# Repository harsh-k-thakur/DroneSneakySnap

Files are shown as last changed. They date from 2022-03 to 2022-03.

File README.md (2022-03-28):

# DroneSneakySnap

This project was build as a part of my quarter studies at University of California San Diego.
This project was executed in a group of two. My partner Rye Gleason and I shared the idea and code together to build an end product. 

This project started with understanding dynamics and kinematics of drone. How does Roll, Pitch, Yaw and Throttle works in an open space.

Once I understood the basic dynamics of the drone. 

I started building with the Hardware. For this I used '''Fusion360''' to create new libraries for my IMU, LEDS and Resistors.
Some of the libraries were directly provided to us, and which are readily available in Fusion360 as well. Thus, understanding the basic schematic of a particular part and utilizing the knowledge of that part to integrate in the main project was important. 
You can see datasheet and schmetics of different electronics component under [datasheeet]('/datasheeet/') folder.

All the necessary things related to Hardware are available in [Hardware]('/Hardware/') folder. Things like Schematics, Fusion360 files, Gerber Files are located in the [Hardware]('/Hardware/') folder. Feel free to check those out.

Once done with Hardware, we started working on software. 
While our Printed Circuit Board (PCB) got printed and came back to us we were given a temporary quadcopter in order to start with programming. 
For the software we had Atmega Arduino Micro-controller on the Flight Controller Board. 
Started the project with basic communication between the remote and the quadcopter using Radio Frequency, testing each motors individually works at different spped using Pulse Width Modulation (PWM).
Integrated throttle control from remote and RF together so that we can control the speed using the remote.

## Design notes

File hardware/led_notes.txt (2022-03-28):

Red LEDs: 
1.95V forward voltage
100 Ohm resistor
22.5 mA current
50.6 mW dissipated by resistor

Blue LEDs:
3.3V forward voltage
51 Ohm resistor
17.6 mA current
15.8 mW dissipated by resistor

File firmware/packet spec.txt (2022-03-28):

1 byte magicnum

1 bit enable
1 bit single/multi motor
2 bit motor select
4 bit parameter select

4 byte parameter value
4 bytes setpoint

parameter options:
1 none
9 PID
1 complementary gain
1 gyro highpass
1 XL LP cutoff

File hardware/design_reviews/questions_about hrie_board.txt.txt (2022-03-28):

Questions from Sample Check LIst

1. Antenna and Antenna Driver
	Everthing looks good for this section

2. Power and Ground
	a. The VBAT and BAT_GND, around motors is less than 3mm, if you dont require current there you can just make your two layers small.
	b. Also you have less than 3mm around your mounting hole towards the board. I don't know if this going to create an issue(we can confirm with professor).
	c. PWM4 line cuts the layer 15 into two planes.

3. IMU
	Everthing looks good for this section

4. Headers
	a. No names gives to breakout header.

5. Microcontroller
	Everthing looks good for this section

6. Power Supply
	2V5 power plane is not under the voltage regulator

7. Motor Drivers
	Everthing looks good for this section
	Can you check thickness of nets the motor driver for me (Rye)!

8. Aesthetics
	a. Board looks fine, but increasing the thickness at the end of the board where motors connects, would help you survive the damage.
	b. Reference designators overlaps near IMU, microcontroller and volatage regulator, try if you can make it work.

9. Mechanical
	Everthing looks good for this section

10. LEDs

11. Checks
	I think there is a blob under antenna which is not required.

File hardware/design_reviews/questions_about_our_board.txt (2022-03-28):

****************
Sample Checklist
****************

Is the trace between the balun and the antenna short (no longer than the corresponding trace in the reference design)?
--> Eaglint wants 6mm, did this pass the auto check?

Is it okay for the antenna to be not on the edge of the board?
--> Signal integrity may be compromised by electrical parts around it, particularly the two parts of the board below the antenna

Should the cutout include part of the MCU?
--> Discussed with us during class

Is the FTDI header oriented so the silkscreen is labels for the pins are on the board and the pins will protrude off the board?
--> Not close to the edge of the board

Does the layout look nice?
--> You can make layer 2 and 15 pours cover the whole board, otherwise the color will be different near the propellor

Double check header orientation
--> Looks different than ours, not sure if that matters

Mechanical ring width
--> Width is 3.2mm, which is much thicker than requirement (1.7mm). Could make it thinner for better propellor clearance.

**********
DRC CHECKS
**********

Trace width error was approved for the balun
--> On ADRV pin in B1, the trace width underneath is much bigger than Professor's video example

Trace width error on pin 58 for the MCU
--> Maybe rewire that pin

****
LEDS
****

24 extra LEDS might be super bright if they can't be dimmed
--> Maybe consider a potentiometer to control brightness
--> Also, resistors are calculated based on max VBAT (4.2V)

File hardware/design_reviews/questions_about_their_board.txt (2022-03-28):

Reviewers: SneakySnap
Harsh (hthakur@ucsd.edu)
Rye (njgleaso@ucsd.edu)
Reviewees: DW
William (wis003@ucsd.edu)
Mingyang (miliu@ucsd.edu)

Questions from Sample Check LIst

1. Antenna and Antenna Driver
	Will the copper DW close to the antenna cause interferece? According to me yes.

2. Power and Ground
	a. The VBAT and BAT_GND, around motors is less than 3mm, if you dont require current there you can just make your two layers small.

3. IMU
	Everthing looks good for this section

4. Headers
	a. No names gives to breakout header. No silkscreen labels on your programming header

5. Microcontroller
	Everthing looks good for this section

6. Power Supply
	2V5 power plane is not under the voltage regulator

7. Motor Drivers
	Everthing looks good for this section

8. Aesthetics
	a. Board looks fine, but increasing the thickness at the end of the board where motors connects, would help you survive the damage.
	b. Reference designators overlaps near IMU, microcontroller and volatage regulator, try if you can make it work. Names and values for C12 and nearby capacitors are a mess, same for C16. C1 and C2 labels will be hidden by the parts you're placing there

9. Mechanical
	a. Grommet ring to board connection is very thin, are you sure it'll withstand a crash?

10. LEDs
	Everthing looks good for this section		

11. Checks
	I think there is a blob under antenna which is not required.

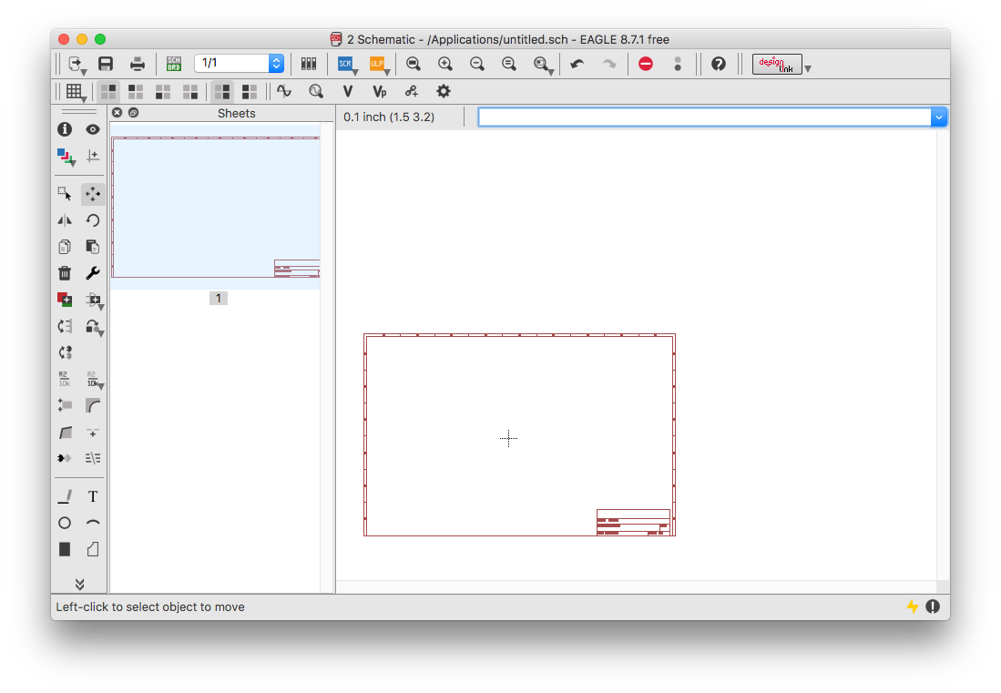
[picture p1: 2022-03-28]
labs/Introduction-To-Eagle/images/schematic4.png

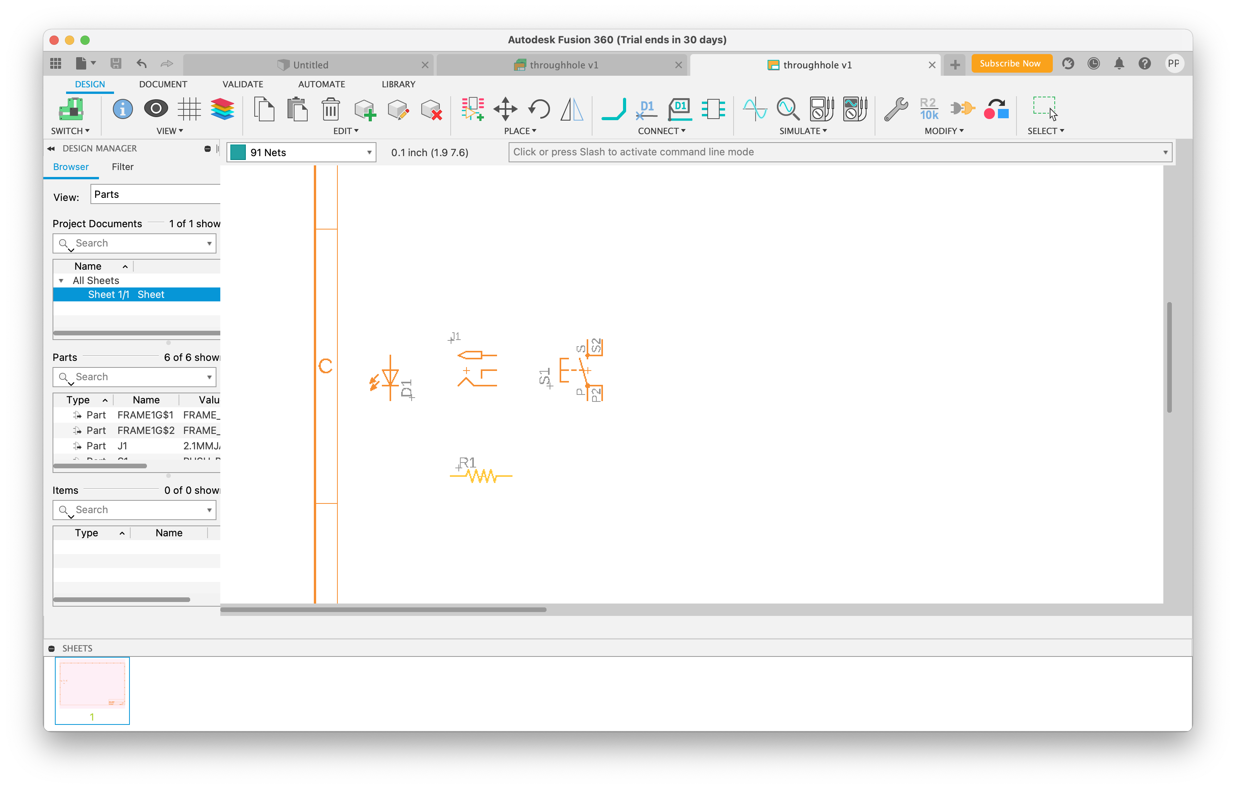
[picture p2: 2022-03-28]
labs/Introduction-To-Eagle/images/schematic6_f360.png

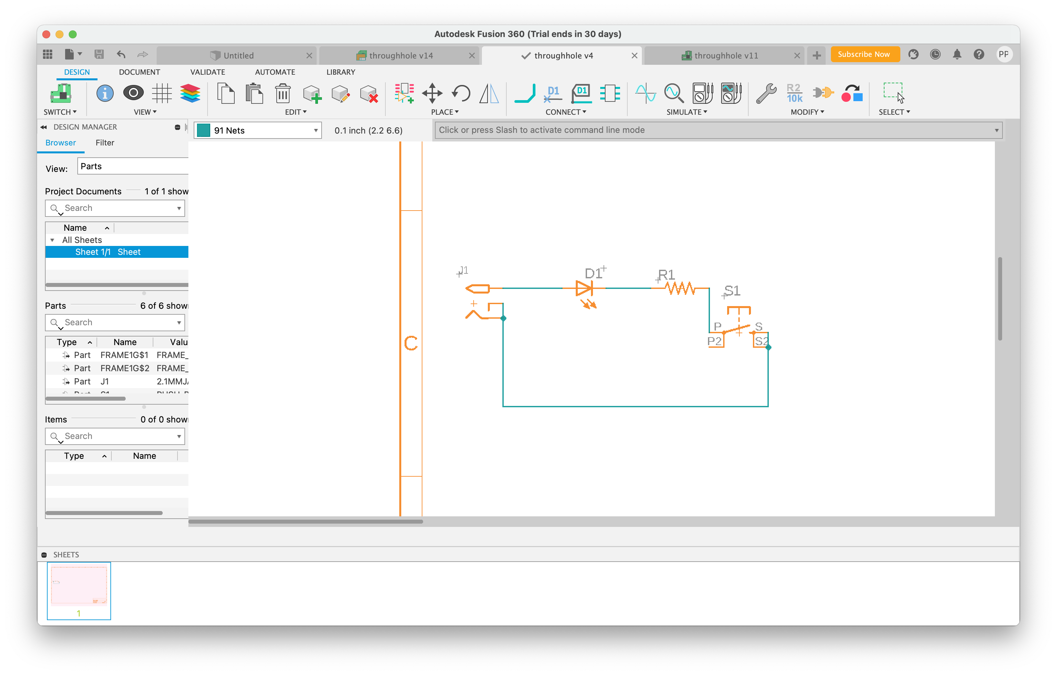
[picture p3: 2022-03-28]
labs/Introduction-To-Eagle/images/schematic12_f360.png

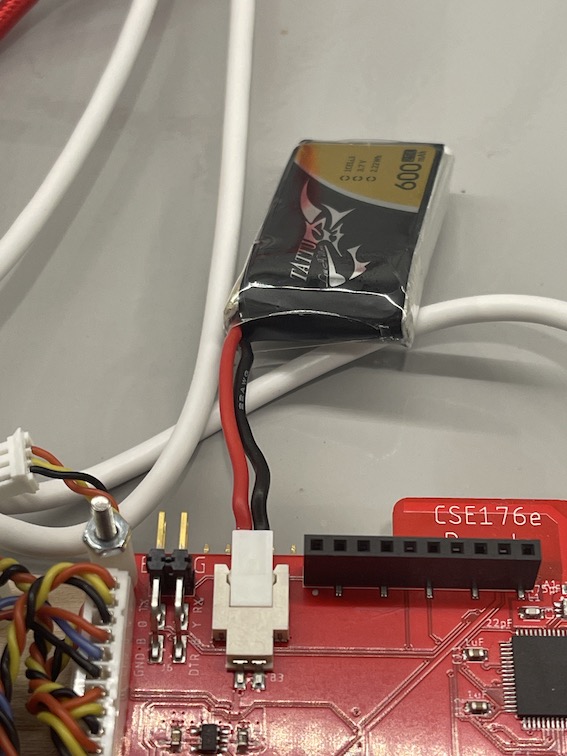
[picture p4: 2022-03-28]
labs/Programming-The-Hardware/images/connect-battery.jpg

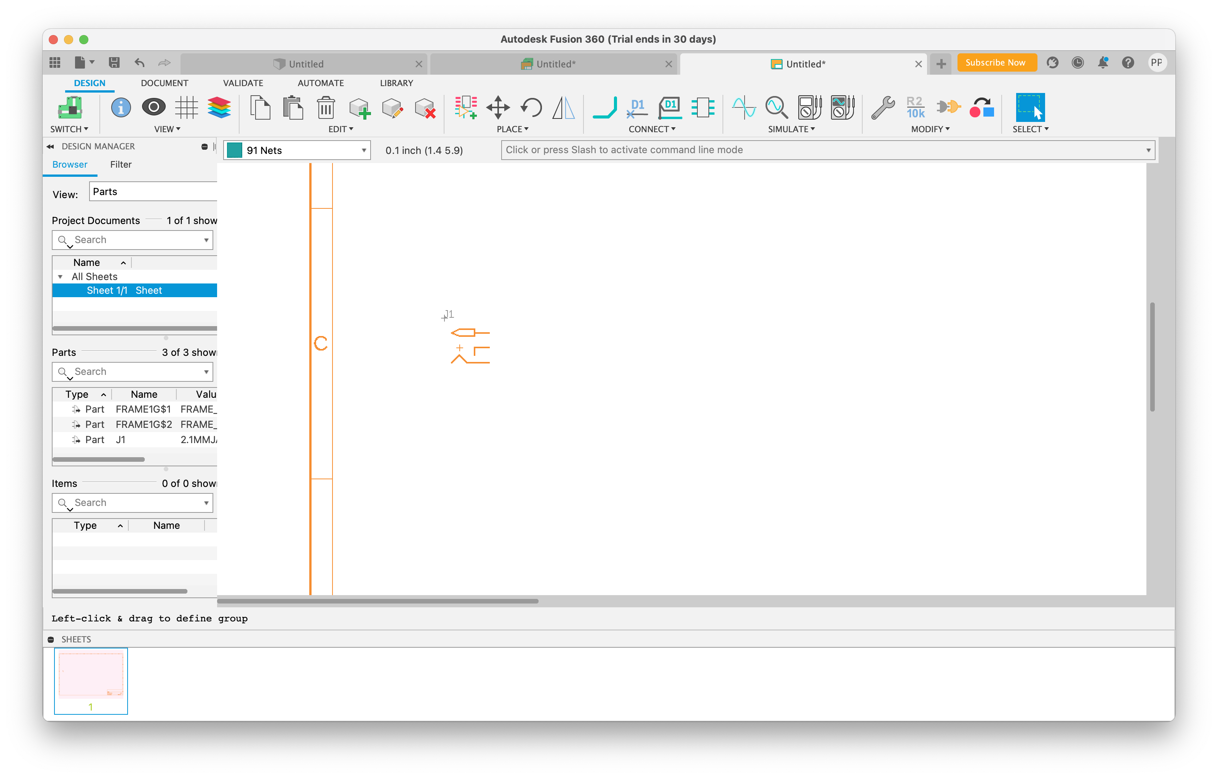
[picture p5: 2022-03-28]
labs/Introduction-To-Eagle/images/schematic5_f360.png

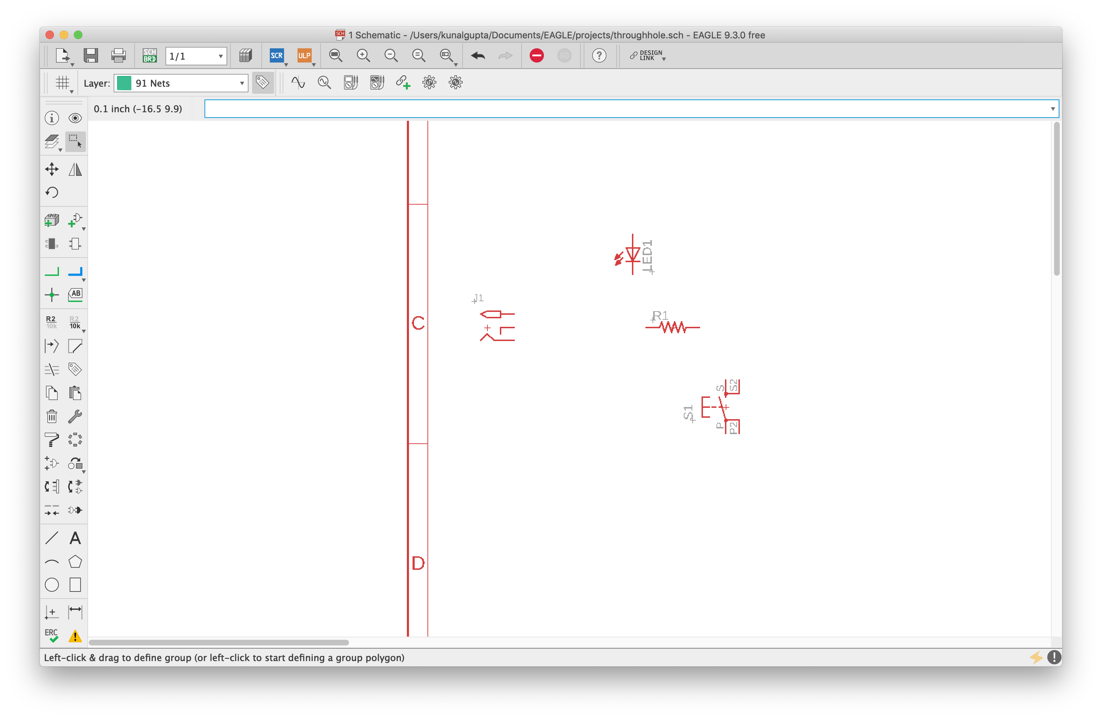
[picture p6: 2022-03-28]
labs/Introduction-To-Eagle/images/schematic6_new.png

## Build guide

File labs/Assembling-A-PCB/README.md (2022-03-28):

# Assembling PCBs

During this lab you will assemble and "bring up" a PCB.  This is practice for assembling and bringing up your quadcopter.

This lab is to be completed on your own.

You will assemble a simple Arduino-compatible board based on the microcontroller we are using for this course.  It's called the Bare Bones Board (BBB).

These instructions apply to assembling your quadcopter and to building your own remote control that you can keep after the class is over.  [Read this](Building-Your-Own-Remote.md) for more details.

Note specific to assembling your quadcopter are [here](Quadcopter-Assembly.md).
## Preparation

Assembling a board (especially your first one) can take a couple hours.  Also, the working time for the solder paste is limited, so you need to work reasonably quickly once you start.

Begin by making sure you have everything you need.  For the BBB and quadcopter assemmblies we will, have everything you need set up ahead of time.

## Safety

The solder paste we use (like all solder paste) is potentially toxic (although it's lead-free).  The material safety datasheet is here: [MSDS](../../Datasheets/NP560_SDS_EN_(V3)US.pdf).

You must take the following precautions:

1.  You must wear eye protection while applying the paste or using a soldering iron.  The makerspace has glasses across the hall from our classroom.  Your own glasses are fine.
2.  You must wear gloves while applying paste and placing parts.
3.  You must not eat or drink while working with solder paste.  During assembly labs, no food or drink is allowed in the classroom.
4.  You must wash your hands before eating or drinking after the lab.

## Applying Solder Paste

### What You Need

1. Blue tape
2. Solder stencil
3. 4 scrap PCBs the same thickness as your board. 
4. 1 large putty knife
5. 1 small putty knife
6. Butcher or craft paper
7. Gloves
8. A magnifier
9. Alcohol in a pump dispenser
10. Kimwipes
11. Compressed air
12. Solder paste
13. Gloves

### Preparing Your Space and Aligning Your Stencil

You need a large, clear space to apply solder paste.

1. It can be messy, so cover everything with a big sheet of butcher or craft paper.  Tape down the paper, so it's not sliding around.
2. Tape down some scrap PCBs so they will hold your board still.  The PCB should be oriented so the stencil aligns with it in "portrait" orienation (tall rather than wide).
3. Align your stencil with your board so the wholes line up perfectly with the pads. This must be very precise.
4. Tape down the right edge of your stencil so you can easily lift it on and off your board like a page of a book.  The tape should be on the right, and there should be clear space for the stencil to lay flat.  
5. Check the alignment again
6. Verify your alignment with course staff.

### Apply Paste

1. Use the narrow putty knife to apply a thin (1cm) bead of paste to the edge of the wide putty knife.
2. Hold the wide putty knife at a 45-degree angle and drag it across the stencil, using firm (but not too hard), constant pressure to apply a thin layer of paste across across the stencil.  Press just firmly enough that there is a thin layer of paste left on the stencil (see photo).  If you push too hard, it will force paste through and slightly under the stencil, which is not what you want.  Move smoothly.  Do not stop.  Make sure you align the knife so it will pass over all the pads on the board.  You can only make one pass.
3. Turn the squeegee over and scrape the extra paste off the stencil with the squeegee almost vertical and held gently against the stencil.  There should be very little paste left.  Again, you can only make one pass.
4. Smoothly and in one motion lift up the stencil and fold it back.  Lifting it up and accidentally dropping it back onto the board is means redoing it.
5. Examine the paste pattern with your magnifier.  Look out for
   * Pads with missing paste
   * Indistict or touching -- even slightly -- paste blobs (esp. on the IMU, microcontroller, and balun).
6. Check it with course staff and point out any problems you spotted.
7. If it looks good, carefully remove your board.
8. If something is wrong, you'll need to remove all the paste using Kimwipes and alcohol and start again.  You can do this many times.
9. You need to be very exacting about paste application.  The solder needs to be very crisply defined.  If it doesn't look good, you'll have to redo it.  Redoing it is not hard, and it's good practice, so there's no point in settling for sub-standard paste application.

**A Stencil**

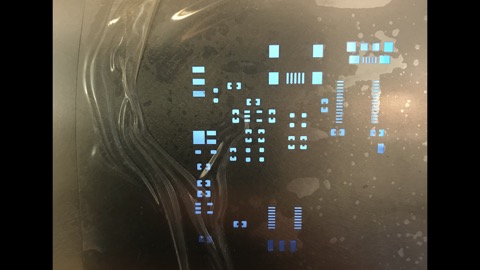
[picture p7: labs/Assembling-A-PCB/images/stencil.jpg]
Stencil


**Poor Stencil Alignment (some holes are dark)**

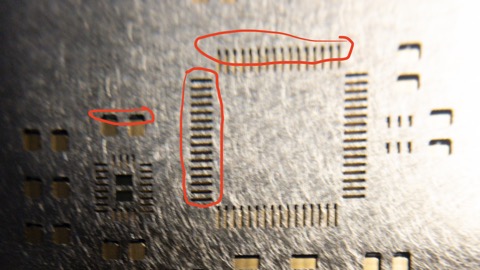
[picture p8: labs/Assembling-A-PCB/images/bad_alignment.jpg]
Poor stencil alignment


**Good Stencil Alignment (all holes are gold)**

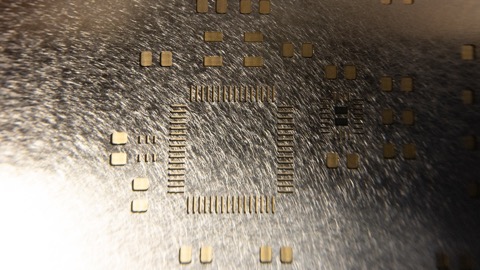
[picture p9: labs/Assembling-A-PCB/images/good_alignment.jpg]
Poor stencil alignment


**Poor Paste Application**

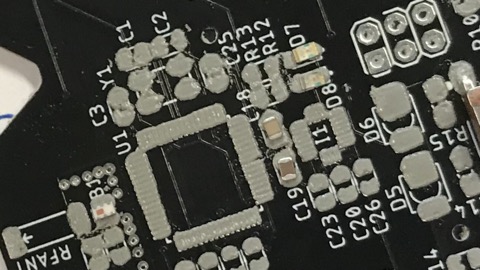
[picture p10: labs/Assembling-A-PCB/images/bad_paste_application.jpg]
Poor solder paste


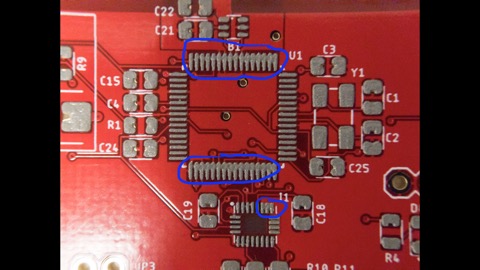
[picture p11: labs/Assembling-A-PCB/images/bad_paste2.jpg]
Poor solder paste


**Good Paste Application**

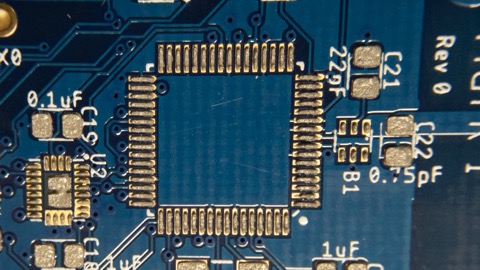
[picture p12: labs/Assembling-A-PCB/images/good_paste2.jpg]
Good solder paste


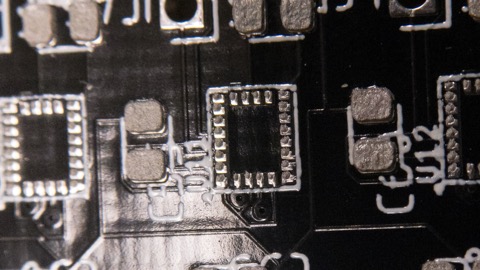
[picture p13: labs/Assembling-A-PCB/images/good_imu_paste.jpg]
Good solder paste


### Cleanup

1. If someone else is going to use putty knifes immediately, you can leave them.
2. If not (or in doubt), clean them by scraping large blobs of paste back into its container and wiping them with alcohol and kimwipes.
3. Wipe up any stray solder paste on the table, *both* sides of the stencil.
4. Blow any remaining solder paste out of the stencil holes with compressed air.

## Placing Components

### What You'll Need

1. A complete part kit for your board.
2. A pair of tweezers
3. A magnifier.
4. Steady hands.

### Get Organized

You need to place parts carefully and precisely.  You also need to work somewhat quickly.  With practice, you can place a board like the BBB in 10 minutes.  You should not take more than an 45 minutes.  Getting organized will help you meet this goal.

1. Get _everything_ you need together at once.
2. Collect all the parts you will need (see below).  For the BBB assembly, you will need 1 packet of each type of part.  They will be laid out for you.
3. Have a clean work area (preferably with a white surface).  The parts are _tiny_.  The less stuff there is around, the less likely you are to lose anything.
3. Allow adequate time.  
    * Paste has a limited working time, and the course staff are not around forever.    
    * For the BBB, Assembly will take ~0.5 hour.  Reflowing takes ~12 minutes.  Something will go wrong, budget an extra ~15min.  
    * So, you shouldn't start assembly unless you have _at least_ 1 hour left in class.
    * For quadcopter or the remote, allocate 2 hours.
5. Eat something before hand.  You need to patient and steady.

Most of the parts come on paper or plastic tape.  We have cut the tape to the right length for you and labeled them.  There are part portions available in the size required for the BBB and for the typical number of parts needed for your quadcopters.  This means you should take 1 piece of tape for each type of part on your board.

The throughhole parts are mostly loose.  Take just as many as you need.

### Placing Parts

1.  Dump the parts from one a packet out on your work surface.
2.  If a part is upside-down, picking it up and dropping it is a good (if probablistc) way to turn it over.
3.  Place the part gently and as precisely as you can.
4.  Once the part is on the board, move it as little as possible.  Moving the parts smears the paste.  The parts will self-align a bit during reflow, so it doesn't have to be perfect.
5.  Don't pick up the board.  You more likely to bump a part if you pick up the board.
6.  Arrange your pile of parts at your board so you don't have to reach over the board, otherwise, you're more likely to bump parts.
7.  Don't mess up.  If something goes significantly wrong, you have to start again.
8.  Do one type of part at a time (e.g., 1uF caps).  For the BBB, you should have exactly the right number of them, so when they are gone, you're done.
9.  Typing `show C1 C2 C3` in Eagle will highlight where `C1`, `C2`, and `C3` are on the board.   You can also say `show C*` to see where all the caps are.  For the BBB refer to the assembly drawings below.
10.  Place the parts very gently onto the board.  It should almost be like you are dropping them.  Do not press them down.  It'll displace the solder paste.
11.  If you think you've messed things up, get the TA or prof.  They may be able to save you...or not.

### BBB Part List

| Part | Qty | Picture |
|---|-----|---|
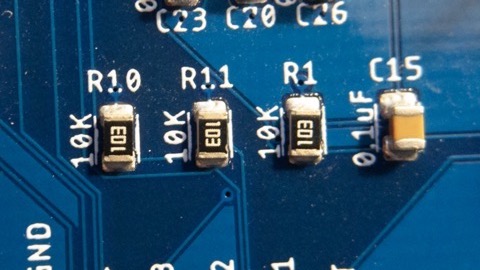
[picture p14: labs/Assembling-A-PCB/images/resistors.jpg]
Resistor
| Resistor 10K Ohm  | 1 | . |
| Resistor 330 Ohm  | 2 | |
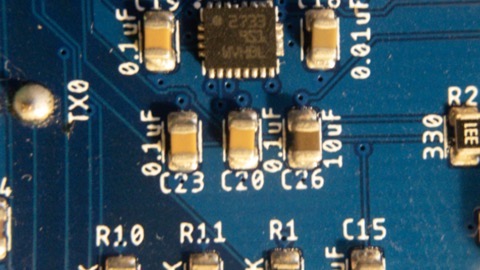
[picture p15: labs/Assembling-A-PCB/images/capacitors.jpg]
Small Capacitors
| Capacitor .75pF | 1 |  |
| Capacitor 12 pF | 2 | |
| Capacitor 1uF | 6 | |
| Capacitor 22 pF | 2 | |
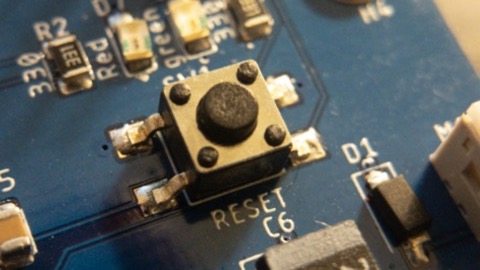
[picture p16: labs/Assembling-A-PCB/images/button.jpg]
Button
| Button | 1 |  |
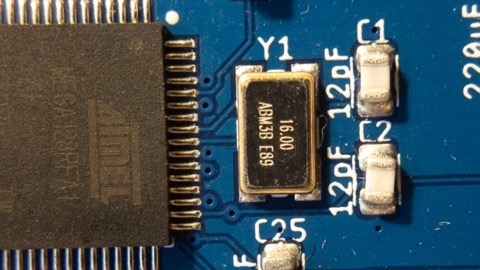
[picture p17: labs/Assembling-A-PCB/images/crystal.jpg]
Crystal
| Crystal | 1 |  |
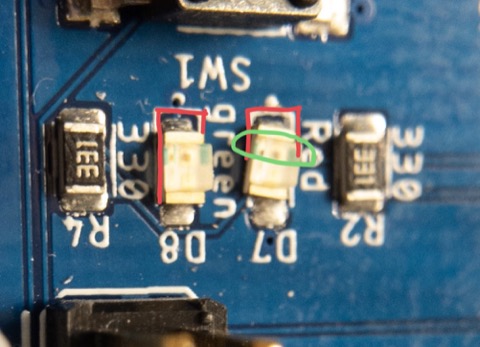
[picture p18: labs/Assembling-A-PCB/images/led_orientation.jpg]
LEDs
| LEDs | 2 |  |
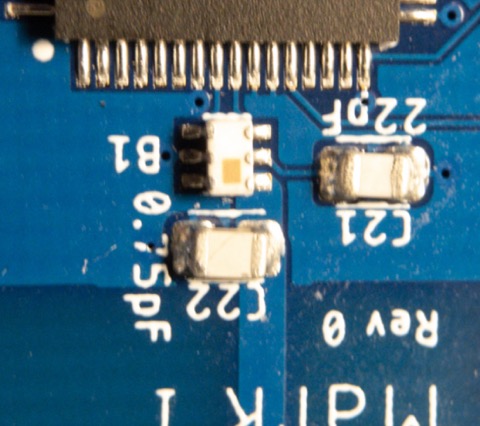
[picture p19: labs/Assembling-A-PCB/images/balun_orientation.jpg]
Balun
| Balun | 1 |  |
| Power Switch | 1 | |
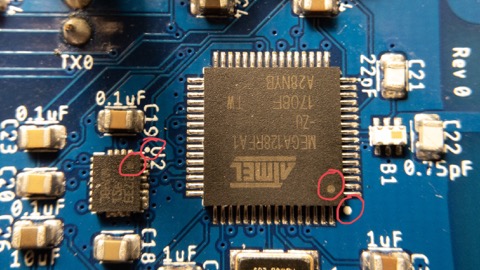
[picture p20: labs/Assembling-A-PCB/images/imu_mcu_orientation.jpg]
Microcontroller
| Microcontroller | 1 |  |
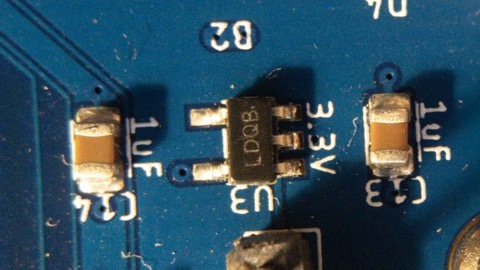
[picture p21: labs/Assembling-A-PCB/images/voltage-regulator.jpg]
Voltage Regulator
| Voltage regulator | 1 |  |
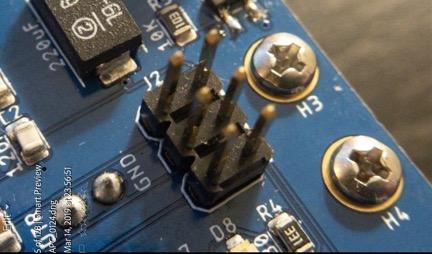
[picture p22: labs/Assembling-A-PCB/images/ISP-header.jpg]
ISP
| Headers(ISP) | 1 |  |
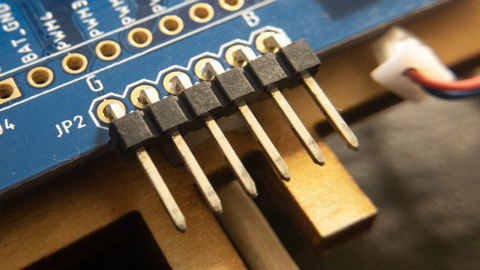
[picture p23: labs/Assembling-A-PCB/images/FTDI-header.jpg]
FTDI
| Headers(FTDI) | 1 |  |
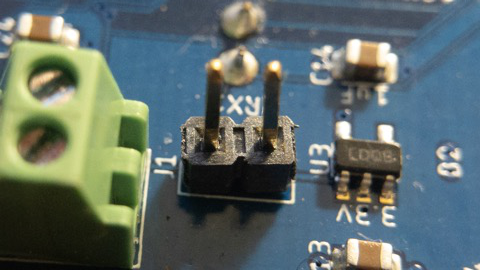
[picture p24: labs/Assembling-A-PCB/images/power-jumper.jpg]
Power jumper
| Headers(Power Jumper) | 1 | ) |
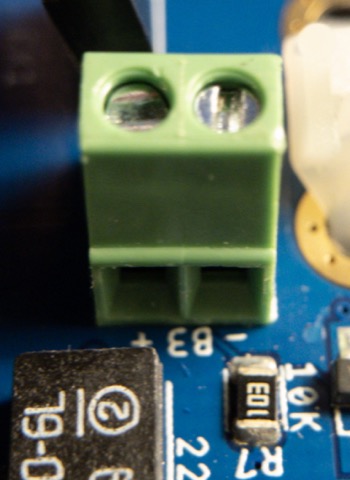
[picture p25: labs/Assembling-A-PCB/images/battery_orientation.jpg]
battery orientation
| Battery Terminals | 1 |   |

### Notes on Particular Parts

I suggest you proceed in this order.  This is roughly from easiest to hardest.

This list covers all the parts on the BBB, your quadcopter, and the quadcopter remote.  Some parts only apply to one or two of those boards.  The parts that are relevant for BBB assembly have a BBB assembly drawing showing where, exactly, those parts should go.

Note that on the remote, there are many parts you will leave unpopulated. Only put parts where there is solder paste.   

In the photos, I've highlighted the polarity markings on the board and the part.

#### Resistors

Resistors

1. These are pretty easy -- a good warm-up.
2. Make sure they are marking-side-up.

##### BBB: 10KOhm Resistors

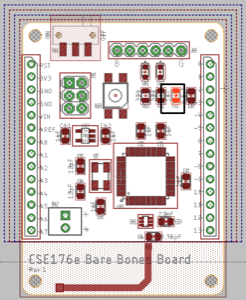
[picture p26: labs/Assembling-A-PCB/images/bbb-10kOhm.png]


##### BBB: 330Ohm Resistors

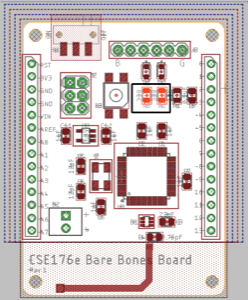
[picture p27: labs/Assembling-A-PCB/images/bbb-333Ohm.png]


#### Capacitors

1.  The small caps are non-polarized, so direction doesn't matter. Capacitors
2.  Align the big caps carefully.  If you get it wrong your board will look ugly.

## 0.75 pF Caps

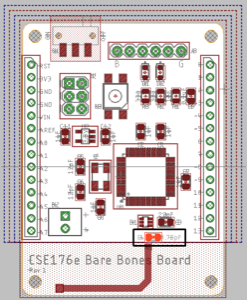
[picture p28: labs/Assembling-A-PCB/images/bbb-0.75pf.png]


## 12 pF Caps

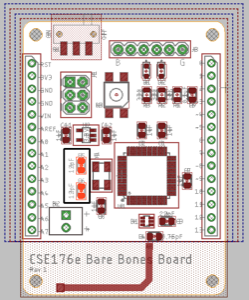
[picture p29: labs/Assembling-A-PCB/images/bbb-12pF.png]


## 1 uF Caps

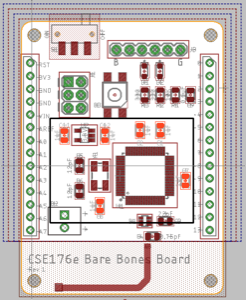
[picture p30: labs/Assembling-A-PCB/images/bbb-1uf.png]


## 22 pF Caps

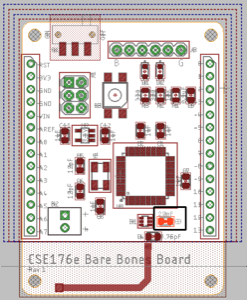
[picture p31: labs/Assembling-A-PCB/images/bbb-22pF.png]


**Good Cap Placement**

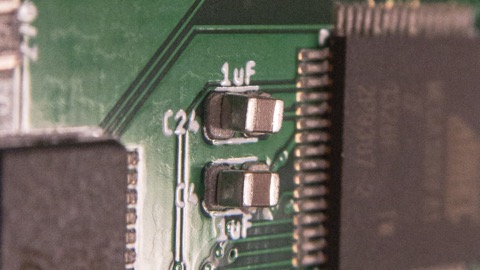
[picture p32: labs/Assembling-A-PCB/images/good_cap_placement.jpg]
Good cap placement


#### Voltage Regulator and Battery Charger.

Voltage Regulator

1. Orientation is obvious (there's three pins on one side and 2 on the other)
2. Be sure not to confuse these two if you are assembly a remote.
3. Only the remote has a charger.

## Voltage Regulator

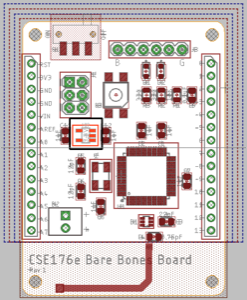
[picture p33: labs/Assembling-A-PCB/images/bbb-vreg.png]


#### Button 

Button

## Button

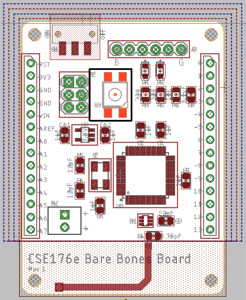
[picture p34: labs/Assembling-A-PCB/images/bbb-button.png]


1. Either orientation is ok.

#### Crystal

Resistors

## Crystal

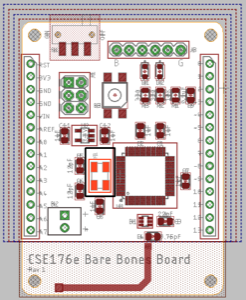
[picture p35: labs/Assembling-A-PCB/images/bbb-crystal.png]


1.  It seems like orientation should be important, but it's not.  The part is diagonally symetric. 

#### LEDs

1. This is your first polarized component, pay close attention or your board will be doomed to darkness.
2. The green line (yes, there really is one) goes near the dot. 

LED orientation

## LEDs

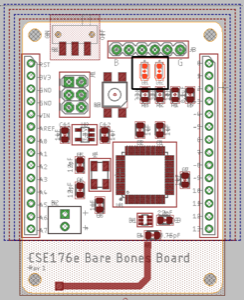
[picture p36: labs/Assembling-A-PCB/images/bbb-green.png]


#### Diodes

1. These are also polarized, but the markings are extremely hard to see.  They are printed black on black.
2. If you hold the diode and look at in the light, one end has a faint rectangular bar code on it.  The other has an "8"
3. The barcode goes near the dot.

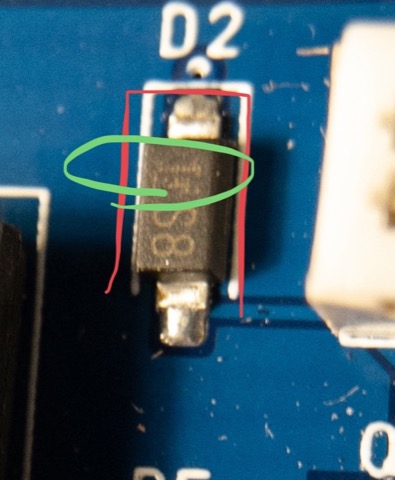
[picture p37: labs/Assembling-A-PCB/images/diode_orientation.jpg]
Diode orientation


#### Balun

1.  The red dot faces up and goes next to the dot.  This means the red dot will be farther from the microcontroller and nearer the antenna.
2.  Pay close attention to the aligment.
3.  Check it with your magnifier.

Balun orientation

## Balun

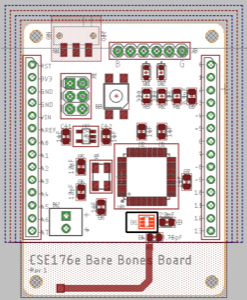
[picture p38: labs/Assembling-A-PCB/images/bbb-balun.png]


#### Microcontroller

1.  Make sure you orient it correctly.  The dot goes next to the dot.
2.  The silkscreen markings fit tightly to the corners of the package, so use them as a guide. 
3.  Once it's down, check the alignment.  If it's not perfect, do not pick it up.  Instead, nudge it every so gently to align it.
4.  The magnifier will help you check alignment.  You can see the pads on the side of the package.  The pins on the package need to be aligned with the patches of solder paste on the board.

## Microcontroller

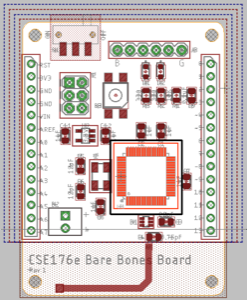
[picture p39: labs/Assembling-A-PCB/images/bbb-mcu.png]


**MCU Alignment**

MCU orientation

**Good MCU Placement**

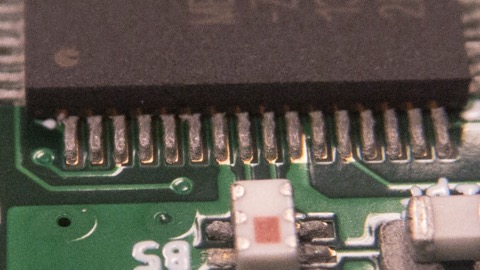
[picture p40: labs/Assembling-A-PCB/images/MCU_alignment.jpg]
Good MCU Placement


## Reflow

### What You Need

1. A TA or professor.
2. The reflow oven.

## Touch Up and Throughhole Components

### What You Need

1. Soldering station.
2. A syringe of flux.
3. Thin, lead-free solder.
4. Swaps and/or a horse-hair brush.
5. Alcohol in a squirt bottle.
6. kimwipes.
7. Blue tape.

### Checking Soldering

**Good MCU Soldering**

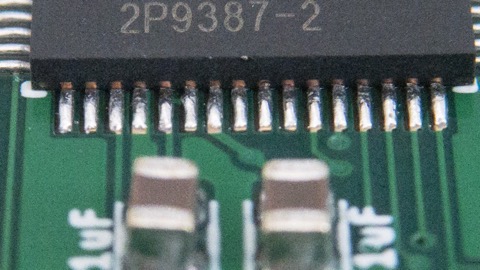
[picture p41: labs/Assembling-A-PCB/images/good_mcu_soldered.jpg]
Good MCU Soldering


**MCU Soldering Requiring Touch Up**

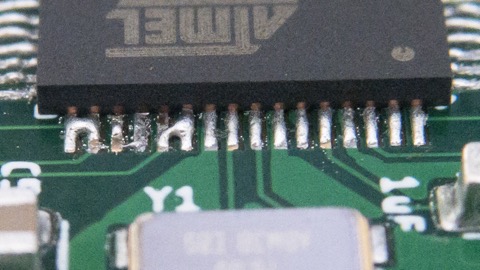
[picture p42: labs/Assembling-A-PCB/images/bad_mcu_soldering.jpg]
Bad MCU Soldering


### Cleaning up Flux Residue

Wire solder has flux in the middle to help the solder flow.  SMD rework requires adding flux manually.  In either case, the result is a yellow-brown, unattractive residue that starts out sticky and hardens over time.

To keep your board looking nice and clean, you should remove it ASAP.  If you have several things to fix, do not wait till the end.  Due it one part at a time.  To clean up the flux, place a kimwipe over the area and squirt rubbing alcohol onto it.  Then, take a hair brush of swap and rub the kimwipe around over the area.  It'll absorb the flux residue.  Repeat once or 
 twice.  Don't be shy with the alcohol, it won't hurt anything.

If you don't have alcohol in a squirt bottle, just get the kimwipe very moist with alcohol and put it on mannually.

### Mounting Throughhole Parts

You'll have to solder the through-hole parts by hand. The process is the same for all of them:

1.  The part goes on the side of the board with the reference designator.
2.  Tape down the part using blue tape. 
3.  The main challenge is getting them straight up and down and not crooked.  Do your best.

We aren't populating the big headers on the BBB to save time in class.

#### ISP Header

ISP

## SPI Header

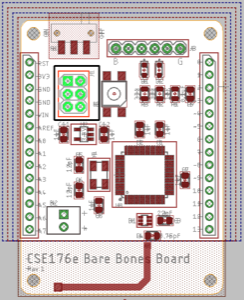
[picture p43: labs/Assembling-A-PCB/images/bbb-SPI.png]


#### FTDI Header

FTDI

## FTDI Header

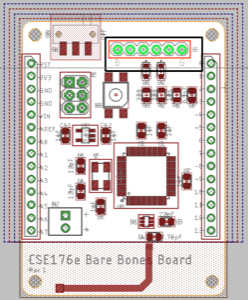
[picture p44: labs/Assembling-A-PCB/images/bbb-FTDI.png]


#### Power Jumper

Power jumper

#### Battery Terminals

1.  Similar to the headers, but orientation matters.  The holes on the side should point toward the '+' and '-' on the board.

battery orientation

### Common Reflow Problems

You should inspect all the parts on your board for problems.  

1. Sometimes solder won't reflow on some parts of the board.  You can tell because the solder paste is rough and not shiny.  To fix it, add a _tiny_ amount of flux and touch it with your soldering iron.
2. Parts sometimes get dislodged during reflow (It's actually pretty windy in the oven).  If only one terminal of the device is still connected, melt that side and lift it up.  If two terminal are connected, see course staff.
3.  You realize you forgot a part.  See course staff for a lesson in mannual surface mount assembly.

## Flashing The Bootloader

Once you've assembled your board you need to [Flash the bootloader and bring up your board](Flashing-The-Bootloader.md)

## Turn in Your Work

Demo you working BBB for the course staff:

1.  Upload a sketch
2.  Blink an LED (using the example code is fine)
3.  Complete the reflection for this lab: https://docs.google.com/forms/d/e/1FAIpQLScKSJucU3BTdXCpcaoRSXui36gL--QQvO2Y9j9LpOaGY0qj-w/viewform

## Remote/Quad only 

#### MOSFETs (Quad Only)

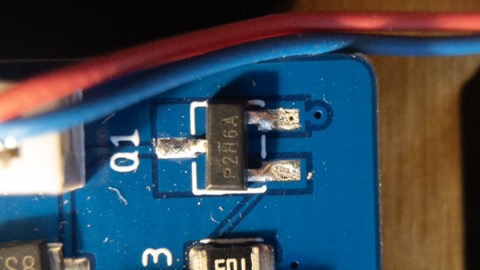
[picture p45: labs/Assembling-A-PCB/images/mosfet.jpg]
MOSFET


1. The correct orientation is obvious, since the package asymmetrical.
2. You need to align the pins carefully.

#### IMU (Quad only)

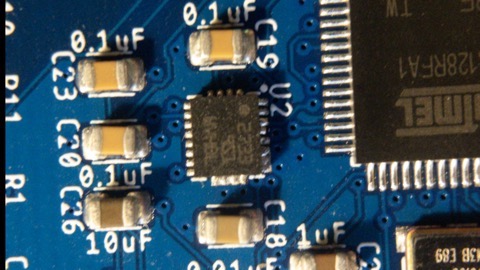
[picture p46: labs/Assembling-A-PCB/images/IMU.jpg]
IMU


1.  Similar to the microcontroller.
2.  The dot goes near the dot. (see image above for MCU)
3.  Use the silkscreen markers to align it and the "drop" it on.
4.  The pads are smaller, so alignment is more important.
5.  Don't fiddle!

#### Motor Recepticals (Quadcopter only)

Motor socket

1.  Orientation is very important.  Removing/replacing these things is really hard. 
2.  The pins are not centered, and part should be oriented so it fits completely inside the silkscreen outline.  If it's backwards it'll protrude on one side.

#### 6-pin Header (Remote Only)

1.  The surface-mount 6-pin header is not hard to place, but it sticks up and is easy to bump, so do it last.

#### USB Receptical (Remote Only)

1.  The key point of alignment are the pins on the back and 5 pads on the board.
2.  Check it with the magnifier.

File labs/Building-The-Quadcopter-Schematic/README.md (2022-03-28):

# Assembling The Quadcopter Schematic

To be completed in pairs.

Check course schedule for the due dates. 

## Skills to Learn

1. Design a schematic to match a written specification.
2. Integrate portions of a reference design into your schematic.
3. Read and understand key portions of part datasheets.

## Equipment, Supplies, and Software You Will Need

1. Create a team in eaglint.  You _must_ do this before clicking the starter link below. <!-- Covid ONly -->
1. The starter repo for this lab: https://classroom.github.com/a/XtjNtfPa. <!-- Covid ONLY --> <!-- Next time reveal this link in eaglint after they have formed the group, so they know what name to use -->
<!-- 1. The repo you started in "Programming the Hardware Lab" -->
2. The `custom.lbr` library you built in previous lab, OR your cloud save for the custom library. From here on out, maintain copies of your libraries on the cloud.
3. Read through the [Fusion Tricks Page](../../Fusion-Tricks.md) and skim the [Autodesk docs](https://help.autodesk.com/view/fusion360/ENU/?guid=ECD-SCHEMATIC) that go over the design tools you will use this lab. 

## Preliminaries

### Setting up Fusion360

The repo for this lab will evolve to hold all the hardware and software for your quadcopter for the remainder of the quarter.

Now would be a good time to start utilizing Fusion Teams. To get started, decide between you and your partner on whose `custom` library should be used. That person should locate the Team online manager in the Data panel on the left:



This will open up a web browser to manage your team. You can edit the name, invite your partner using their email, and have shared access to a cloud version of your library! Rename it as `custom_<name>` so that the versions from both team members can co-exist. If you run into issues with one partner's library, you can always import your other library into Fusion360, just be sure to maintain them using the cloud! You should not reference local versions of `.lbr` files, and you should only export them when you are ready to submit.

To clean up local copies of previously-used `.lbr` files, and to remove unnecessary third-party libraries, you can remove them using the library manager (make sure to keep your team's library in use):



Feel free to remove all libraries except for your `custom` team library from last lab.

### Make Fusion360 Easier to Use

By default, Fusion360 comes configured with a bunch of libraries that can make it hard to find the libraries we are using for this class. This is controlled by the directories Fusion360 is setup to look in for library and other files. You can change the directories by selecting `User->Preferences` (upper-right corner) and then selecting `General->Electronics->Directory`.

To keep Fusion happy and make it easier to access and update libraries in the cloud, remove all the local folders Fusion is configured to look in for libraries. For Design rules and CAM files, I suggest the following settings:

* Design Rules: `<path to>/QuadClass-Resources/Eagle/DRU`
* CAM Jobs: `<path to>/QuadClass-Resources/Eagle/CAM`

## Assembling the Schematic

You’ll build quadcopter in the cloud starting from a new Fusion360 electronics design called `quadcopter`. When creating this design, make sure to save it to the right team. 

In this lab, you will create a schematic associated with this design, to be exported to the folder `hardware/quadcopter.sch`. Feel free to review [Lab 1](https://github.com/NVSL/QuadClass-Resources/tree/master/labs/Introduction-To-Eagle#exporting-files) for a refresher on exporting. You'll assemble the design by studying reference designs and the datasheets for the components you will use.

We will be sharing a library with you via the cloud called `quadparts_prebuilt`. You will be reusing your `custom` library from last lab, and in this lab you will also create a new library called `LEDs`. These should be the only 3 libraries you use to assemble your schematic,  Fusion360 comes with a bunch of built in libraries but they are off limits.

### General Schematic Style Guidelines

Here are the course style guidelines for schematics. Your schematics must adhere to these guidelines.  If you don't, Eaglint will give warnings and we won’t accept the design.

1. All visible net and component names must not have “\$” in them. When Fusion360 automatically generates names for nets and components it includes “$”. This is fine if the name is not visible (e.g., on an anonymous wire between two components), but if you it shows up on your schematic, you should give it a nice name like `CTRL` or `SCL`.
2. By convention power supply symbols point up, and ground symbols point down.  Neither should ever point to the side.
3. Nets should not cross each other unless they are electrically connected.
4. Nets should only be drawn at right angles.
5. Fusion360 embeds libraries in the `.sch` and `.brd` files. Make sure that you are keeping libraries up-to-date with  `Library->Update...` or `Library->Update All`. We won’t accept designs with inconsistent libraries.
6. Include a frame around our schematic.  Use device `FRAME_B_L`.
7. Use lines in `Info` layer to divide the frame into logically related regions (e.g., the IMU, the power supply, and the microcontroller). See the BBB schematic below for an example. Drawn nets shouldn’t cross these boundaries.
8. Use drawn nets connect components that are closely related (e.g., between the caps and the microcontroller in the BBB schematic)
9. Use named nets to connect separate “sub units” of your schematic. For instance, use drawn nets to connect all the capacitors to your IMU, but use named nets to connect your IMU to the microcontroller.
10. You should not use any libraries other than `quadparts_prebuilt`, your `custom_*`, and your `LEDs` libraries.
11. Schematic symbols and wires should all be aligned to 0.05in grid (or, if you like, a 0.1in grid).
12. Labels for nets (created using the 'label' tool) should need to placed on the net they label.  This means the label's location (which is marked with a gray '+') needs to be on top of a corner or end of the net.  This guards against "drifting labels" that seem to be attached to another net.

### Selecting Parts

The `quadparts_prebuilt` library has lots of parts in it, many of which you won't use.  I've provided specific guidance about which options to select below.  For resistors and capacitors, you need to use 0805 parts not the smaller and harder-to-place 0603 parts.  If the resistor you need is not available in 0805, you'll need to create it.

### The Microcontroller

Here's the schematic for a board called the Basic Breakout Board (BBB).  It uses the same microcontroller as your quadocpter, but it does not include the voltage regulator.  It's the reference design for your microcontroller and the radio.  The design also includes the 1x6-pin programming header you can see on the bottom of the FCB.  YOu don't need to include that header in your design. 

Why did I give a picture of what you need to build?  Because reference designs are a very common practice in real PCB designs.  The most reliable way to convey design requirements is to provide a working design.  Why reinvent the wheel?

Microcontroller schematic

You should use the schematic as a guide for constructing the microcontroller portion of your schematic.  Build it from parts from `quadparts_prebuilt` libbrary:

1.  Use one of the `ANT_PCB...` variants for the antenna.  There's a left and right-handed version.  Depending on your ultimate board design, you might want one or the other.
2. `B1` is a 'balun'.  Pay attention to the pin numbers.
3. Use the `0.45x0.45` button.
4. Replace one of the green LEDs with your red LED.
5. You can use either variant for the `AVR_SPI...` header.  The surfacemount one takes up more space (see it on your remote, under the LCD).  The throughole one is more compact.
6. You won't need the FTDI portion of the design.
6. Do not connect the power pin on the ISP programmer/Bootloader header.

You might notice that some of the symbols for the parts seem backwards.  This is because they are 'mirrored'.  There's a mirror tool or your can mirror parts by editing their properties with the `info` tool.

There are some changes you will need to make to this schematic based on what's required by the other components.  This is just a starting point for your circuit.

If you have questions about the parts attached directly to the microcontroller (including the radio), the first place to turn is the microcontroller datasheet.

### Programming Header

Your quad will use a 4-pin programming header to load code into the MCU.  You won't need the FTDI portion of the reference design.  It's a little fancy since it allows you to insert the cable from either top of the board _or_ the bottom.  To this end, use the `-FEMALE-SMD-BOTTOM-ENTRY` part from `quadparts_prebuilt`.  The four signals must appear in this order:

1.  Serial TX
2.  Serial RX
3.  GND
4.  Reset

These are a subset of thesignals that connect to the FTDI header in the microcontroller reference design.  You don't need the FTDI header.  Note that you do need the 0.1uF capacitor between the reset line and the reset pin on the programming header.

### The IMU

The IMU datasheet contains all the information you will need to use connect the IMU to the microcontroller. A few things to keep in mind:

1. The IMU datasheet is not the best.  If something doesn't make sense search the pdf.
2. There are actually two logical devices in this package: the accelerometer/gyroscope (referred to as 'A/G' in the datasheet ) and the magnetometer ('M').
3. Both devices will operate in I2C mode only and connect to microcontroller via I2C, so you can ignore the stuff in the data sheet that refers to SPI.
4. You must follow all the recommendations regarding external capacitors attached the IMU.
5. You will need to take care to configure the IMU's I2C addresses. It has two: One for the gyroscope and accelerometer and another for the magnetometer. The address for the gyro and accelerometer should be set to `1101011`. For the magnetometer it should be `0011110`.  You should read the datasheet to learn how to do this.  Note that there is an inconsistency between Table 2 and Tables 19 and 20.  Tables 18 and 19 are correct.
6. Power supply voltage and IO voltage will be 2.5V in our design, so connect them to `2V5`.
7. We aren't using the interrupt features, so you can leave `INT_M`, `INT2_A/G`, `INT1_A/G`, and `DRDY_M` disconnected.
8. `DEN_A/G` should be connected to `2V5`.

Most of the information you will need is Section 5 of the datasheet. 

A thing to know about datasheets: They almost always (although, frustratingly, not always) tell you everything you need to know.  They don't, however, make it easy.  You need to read carefully and thoroughly.  You can't skim the datasheet and expect to know the details of how to connect each of the pins to configure the IMU properly.  You actually need to read through the tables and the text, there are specific answers to most questions you might have in there.  Most facts appear exactly once in the datasheet -- it will be written in text or a table, but not both.

### The I2C Bus

Your MCU will communicate with the IMU via I2C.  This means you must connect the IMU to the MCU via the `SDA` and `SCL` lines.  You should "pull up" these lines to `2V5` by connecting them to `2V5` using 10kOhm resistors.

### The Motor Driver 

Here's a picture of the motor driver circuit:

Motor Driver

Build four copies to drive the four motors you'll need.  All the parts you need are in `quadparts_prebuilt` or your `custom` libraries.

1. Use the `-SMD-SOD123` diode in the library.
2. Use the `-MOLEX-SMD` variant of the `MOTOR_PADS_GND` device of the motor connector.
3. Use your MOSFET, of course.

The ground pin on the motor pads is not actually connected to the motor.  It just goes to the metal "feet" that hold the connector down.  You can see them on your FCB.

You'll need to connect the PWM control lines to suitable pins on the microcontroller. The suitable pins are marked with "~" on microcontroller's schematic symbol.

You need to include one 47uF decoupling capacitor between `VBAT` and `BAT_GND` (just one; not one per motor).  It's to help absorb switching noise from the motors.  Note that 47uF capacitor in the library is polarized.  In the schematic the curved "plate" on the symbol should be connected to ground.

### The Power Supply

The quadcopter draws power from from a LiPo battery that nominally provides between 3.7 and 4.2V. This voltage is too high for the IMU and the microcontroller.  Also, the motors (which we will power directly from the battery) will create all kinds of noise on both the battery supply and ground rails.  To solve both of these problems, we will use a low-dropout (LDO) voltage regulator to provide a stable 2.5V power supply to the IMU and the microcontroller.

As a result, your quadcopter will have two power rails: An unregulated power rail (called `VBAT`) that provides power to the motors and input of the voltage regulator and is driven directly by the battery, and a regulated supply driven by the voltage regulator (called `2V5`).

The power supply for quadcopter needs to contain the following parts:

1. The battery. This is the `BATTERY` device in `quadparts_prebuilt`.  You need to use the `-SMD-TH` variant.
3. A LP3985-series 2.5V regulator (see device `TPS73633-DBVT`.  Don't use th 3.3V or 3V versions).

Check the votage regulator datasheet (in `Datasheets`) for guidance about what kind of capacitors to connect to the regulator and how.  Wire the enable line to `VBAT` and don't connect anything to `NC/FB`.

You will also incorporate a power switch for the quadcopter.  The switch will connect the `EN` pin of the voltage regulator to `VBAT` when it's turned 'on' and connect `EN` to `GND` when its turned 'off''.  Use the `-SMD-EDGE` variant of `POWER-SWITCH-MFS201N-9-Z` for the switch.

You'll note that the output of the voltage regulator has decoupling capacitors on.  This keeps the voltage regulator stable and filters out noise on the output. Experience shows that quickly turning on the motors can causes the output of voltage regulator to drop enough to reboot the MCU.  Add an additional 47uF decoupling cap (the same one we use for motors) to the output of the voltage regulator between `2V5` and `GND` to prevent this.  Note that the 47uF capacitor is polarized.  The flat plate should connect to the positive voltage, and the curved plate to ground.

To the extent possible, we need to isolate the the IMU and the microcontroller from the noise that the motors will create on the power supply lines.  The motors will cause noise on both their power supply ( `VBAT` ) and ground return lines, so we will provide them with separate power and ground lines.  For the power line, this is easy: Just connect the power supply for the motor drivers directly to the battery's positive terminal.

For the ground line, it is more challenging, since all the devices on the quadcopter must share a common ground reference. The best we can do is to structure our schematic so that we can exercise tight control over how the ground line is laid out on our PCB.  To do this, create a separate ground net that connects the ground terminals of motor controllers to each other and the negative terminal of the battery (call it `BAT_GND` and use the `BAT_GND` device in the `quadparts_prebuilt` ).  Then connect the digital ground (i.e., the ground that connects to other components, aka `GND` ) to the battery ground using a schematic component called a "net bridge" (see below). We will see in the next lab how we can use this structure to isolate the digital components. (This is a very important step, and we added it to fix problems that occurred in all but one of the quadcopters we built in this class the first year it was offered). 

A "net bridge" is a PCB part whose only purpose is to electrically connect two nets in a schematic while keeping the nets separate in schematic (i.e., the two nets keep their own names). To create a net bridge, create a device with a footprint that consists of two SMDs that touch one another and a sensible schematic symbol for what is, in essence, a wire.  Put it in your `custom` library.  The SMDs can be very small (e.g. 0.5mmx0.5mm). Remove the `tStop` and `tCream` on the pads, since we won't be soldering anything to them.  You don't need `tKeepout` anything in `tPlace` for the net bridge.  If eaglint complains, just explain that it's not necessary since it's the net bridge.

Use bridge to connect `BAT_GND` and `GND`.

#### Basic Principle: Decoupling

Your quadcopter is full of transistors (small ones in your microcontroller and big ones in your motor drivers), and as they switch they cause noise on the power and ground planes. Noise on the power line can cause digital circuits to stop working (because 1’s start looking like 0’s) and noise on GND can cause all kinds problems because all voltages are measured relative to GND.

The minimize this noise, we want to increase the capacitance of the power and ground planes. One way to think of capacitance is as a resistance to changes in voltage, so adding more will reduce noise (which is an unwanted change in voltage).  Small capacitors can filter out high-frequency noise, while larger capacitors filter out lower-frequency noise.

There are two ways to add capacitance.  The first is to add capacitors.  The IMU and the microcontroller both describe the number and kind of decoupling capacitors you should incorporate and they tell you to place them as close as possible to the power and ground pins on the device.  This is because, to be most effective, the extra capacitance we add needs to be as close to the source of the noise as possible (to minimize resistance and inductance between the cap and the device).

The second way to add capacitance is to build a capacitor into the board. A capacitor is just two layers of metal separated by an insulator.  We can easily construct this in a PCB by laying down metal in two layers on top of eachother, and connecting one to power and one to ground. The result is a very small capacitor but one that we can put nearly everywhere on the PCB (so it will be a close as physically possible to the devices).  In our design this capacitance is not critical, but in higher-speed design, it is critical to filtering out the higher-frequency switching noise.

### Breakout Headers

You will face a couple challenges in bringing up your board and it's good to plan for them now.  Do this by adding two debugging headers to your design.  "Headers" are exposed connections to signals on your board.  You can attach pins or sockets to them as needed to help in debugging.

#### Signal Breakouts

When your quadcopter comes back from manufacturing and you assemble it, some debugging may be necessary and that may include the need to measure what's going on in different parts of the circuit. To make this easier, I suggest including a debugging header in your design.

A debugging header is a set of pins that connects key signals to pins that you can easily probe during debugging. I suggest including the following signals:

* `GND`
* `BAT_GND`
* `VBAT`
* `2V5`
* The control lines to the four motors
* `SDA`
* `SCL`

There's a 10-pin header in the library you can use for this.  You can also break up the debug header into smaller headers. For instance, you could put a 3 pin header next to each motor with `VBAT`, `BAT_GND`, and the control line. It's always a good idea to include a ground on each debug header.

Debugging headers can be a little dangerous to use, because it can be easy to accidentally create a short circuit between two of the pins when you are debugging (e.g., by touch both pins with a probe).  This is especially dangerous if you connect a power net and a ground net.  To avoid this, intermingle the PWM, SDA, and SCL lines with the power and ground lines, so that no power pin is next to ground pin.

#### IMU Rescue Header

Soldering the IMU is hard enough that it causes a fair number of
quadcopters to fail.  To guard against this, add a header that will
allow you to connect this breakout board
(https://www.adafruit.com/product/3387) to your quadcopter.  You need
four pins: `2V5`,  `SCL`, `GND`, and `SDA` (not necessarily in that order.  Look at the board it must connect to.), which are conveniently
located together on the breakout board.  Use the 4-pin female header
in `quadparts_prebuilt`.

If you feel like being efficient, you can leave `SDA` and `SCL` off the signal breakout header, since they are on the rescue header.

### Some LEDs

You should also add some LEDs to your design. There are several reasons to add LEDs to your design:

1. It'll make it easy to tell which end of your quadcopter is the front.
2. They look cool.
3. They can provide information about what's going on in your flight control software.

There are several options for powering and/or controlling LEDs:

1. You can connect them directly to battery power and battery ground. In this case, you can't turn them off, but they can be very bright.
2. You can connect them to pins on the micro controller.  If you use a digital pin, you can turn them on and off.  If you use a PWM pin, you can control their brightness.  In either case, you must size the resistor properly to limit the current through the LED to 8mA (the limit on the per-pin current on your microcontroller).
3. You connect them to battery power and turn them on and off using a transistor connected to a microcontroller pin.  Depending on the pin you use, you can turn them on and off or vary their brightness. The transistor we use in the motor controller should work fine.  If you do this, you can drive multiple LEDs with the same transistor and pin.

If you drive LEDs with a MOSFET, you should include a 10kOhm pull-down resistor to `GND` on the gate of the MOSFET.

Regardless of which approach you take, you will need to pick out your LED.  To do this, go to http://digikey.com.  And enter LED into the search field.  You'll see a bunch of results.  Likely candidates for smaller LEDs are to be found under "LED Indication - Discrete," while brighter LEDs can be found under "LED Lighting - White", "LED Lighting - Color".

You'll note there are a dizzying array of options (at this moment there are over 20,000 different indicator LEDs available). Digikey presents you with a decent searching interface. Go exploring! Things to keep in mind:

1. Any LED you choose needs to be available in small quantities (the "minimum quantity" column should say "1").
2. The need to be at least 0805 (1.25mm x 2mm).
3. They need to be reasonably cheap: no more than $1 per LED.
5. If you are going to drive the LEDs directly with a microcontroller pin, you must limit current to 8mA and you should make sure that the LED will actually light up with 8mA (many bright LEDs will not).
6. They need to be compatible with the power supply you are going to use: 3.7-4.2V if you use the battery. 2.5V if you are going to drive them from the microcontroller.
7. Their current draw needs to be within the limits of how you are powering them.
	1. The microcontroller limits how much current each pin will supply.
	2. The microcontroller consumes some current, as does the IMU (check the datasheets).
	3. The voltage regulator has limits on how much current it can provide.
	4. Make sure that voltage regulator can handle all your LEDs in addition to the microcontroller and the IMU.
	5. If you are powering them with VBAT, limit total current draw for all your LEDs to 500mA.
8. The current draw depends on forward voltage. The LED datasheets will contain some graphs that relate voltage to current and current to brightness.  Pay attention to them to make sure that a) you aren't drawing too much current and b) your LEDs will light up.
9. There are many different parameters to consider: Color, brightness, viewing angle, etc. You'll need to go learn about these by reading the datasheets, etc.
10. You will probably want surface mount parts, but you can also use through-hole if you want.
11. Digikey lists the typical forward voltage on the web page. The LED will work with larger or smaller voltages (up to a point. See the "absolute maximums" section of the datasheet for limits).
12. If the forward voltage of the LED is much lower than the supply voltage, you'll need a large resistor to limit the current. Alternately, you could put two (or more) LEDs in series. The total voltage drop across the LED(s) and resistor needs to be greater than or equal to the supply voltage.
13. You can use RGB LEDs, too. Checkout the datasheets for details.

You'll need to build the library entries for the LED you want to use and then integrate them into your schematic.  You'll also need to include a current-limiting resistor.  You'll need to use Ohm's law to calculate the correct resistor value (here's a tutorial: http://www.ohmslawcalculator.com/led-resistor-calculator).  You will also need to be sure that resistor can handle the amount of power it will need to dissipate (see the datasheet). If our libraries doesn't include an appropriate resistor, you'll need to add one from the same family of resistors we are already using (check the datasheet for the resistors in `quadparts_prebuilt`).  Make sure it's available in small quantities on Digikey.  Put the new resistors in `custom`.

One thing to keep in mind is that most LEDs are extremely bright when driven at full current. Indicator LEDs can be driven very gently and still be visible.  LEDs added for visual effect can be driven harder, but they can easily become so bright that you can't even look at your quadcopter without being blinded.  For this reason, any LEDs that you want to be bright need to be attached to PWM pins, so you can moderate their brightness.

Once you have picked your LEDs, document your LED design using text in the `Info` layer in your schematic.  For each type of LED, you should note its forward voltage, the resistance of the current limiting resistor,
and the current you expect to flow through the LED. 

Feel free to get creative with the LEDs!  Smilely faces.  Simulated space ship engines.  Aircaft "running lights".  Dance party.  Ground effects.

Put the LEDs devices/footprints you create in a new cloud library called `LEDs`. Reuse the LED symbol from `quadparts_prebulit` or your `custom` libraries. 

The footprints/devices you build need to meet all the standards described in `Building Parts in Fusion360 Lab`.

Add an attribute called `CUSTOM` to the variants you create.  It should be constant but without a value.  This will ensure they get ordered.

### Eaglint 

Your design needs to pass http://eaglint.nvsl.io, so commit your design, submit it, and fix the problems it finds.  Remember, each time you run a full check with the tool it lowers your grade on the lab, so you need to check your design carefully before submitting.

### Things to remember

1. Remember to sync your libraries with your schematic: `Library->Update All`.

### Things to Submit

Include these in your github repo:

1. Your `hardware/quadcopter.sch`.
2. Your `hardware/lbr/LED.lbr`.
3. Your `hardware/lbr/custom.lbr` (maybe renamed to `custom_<name>.lbr` and maybe two of them)
5. Datasheets for your LEDs in `hardware/datasheets/`.

Feel free to consult [Lab 1](https://github.com/NVSL/QuadClass-Resources/tree/master/labs/Introduction-To-Eagle#exporting-files) for export guidelines.

Submit it to Eaglint: http://eaglint.nvsl.io.

For this part of the lab, human review will succeed instantly, if you have no errors or warnings.

Once it passes, create a tag called "initial-schematic" Be sure to make it an "annotated" tag and push it to your repo (https://git-scm.com/book/en/v2/Git-Basics-Tagging). Verify that it is visible on github.

## Turn in Your Work

"Perfect" score: 10

Initial points: 12

Quick checks are free.  Full checks cost 0.5 points.  Submitting for human review costs 0.5 points.  Each day late costs 1 point.

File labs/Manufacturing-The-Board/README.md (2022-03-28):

# Tape out

To be completed in your groups.

Check the course schedule for due date(s).

## Skills to Learn

1. Prepare CAM files for submission to the manufacturer.

## Equipment, Supplies, and Software You will Need

1. Eagle
2. Your design review documents.
3. Your PCB schematic and layout.

## Tasks To Perform

### Finalizes your Design

This is your final chance to fix any problems. You should perform another design review yourself, after reviewing the checklist in the previous lab.

You should also be on the look out for any moments when a small voice in your head says “hmm… I’m not sure about that.” When that happens, ask about it on Piazza. Include a screen capture of the relevant parts of your board.

Follow the guidelines in the board layout lab under the heading "Generating Gerbers" to generate your final cam files.

### Commit Your Final Design

Commit your final design to your github repo. This should include

* Your updated `hardware/quadcopter.sch` and `hardware/quadcopter.brd`
* Your final `hardware/quadcopter.cam.zip`. Please be _certain_ that this the right cam files. I suggest deleting all cam files in your repo, regenerating them and zipping them up. Be sure to commit.
* A file called `hardware/metadata.txt` that has the following:

    1. Color you want your quadcopter to be. Choices are: Green, White, Blue, Black, Red, or Yellow.
    2. Silkscreen colors: White, Blue, Black, Red, Yellow (different than your board color).
    3. The dimensions of your board in mm.

Submit it via Eaglint. You can expect the reviews to be quite stringent.

### The Ordering Process

**YOU DO NOT NEED TO ORDER YOUR BOARD. I WILL DO IT.**

This is just here for your information.

Some of you have asked about the ordering process.  We are using https://www.pcbcart.com/. To build the boards, you need to create an account, and then go to cart and “add item” to place an order.

Basically, you just upload the zip file of your cam files, and select some options, and pay with a credit card. Here are the options we will be using:

* 4 layers
* 5 boards (you’ll get 5 copies of your board)
* thickness 1.6mm
* color: based on your `metadata.txt`
* Surface finish: LeadFree ENIG
* Copper thickness: 1oz
* Gold fingers: no
* Material: FR4

A list of their capabilities is here: https://www.pcbcart.com/pcb-fab/standard-pcb.html. This is what get transcribed into the DRU file.

You can order a stencil as well (based on your `.crm` gerber).  However, I usually order stencils from https://www.oshstencils.com/.  They are smaller and a little easier to work with.

We have also had good results with https://jlcpcb.com/.

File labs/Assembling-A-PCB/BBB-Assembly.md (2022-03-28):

# Bare Bones Board Assembly Drawings

Below are the assembly drawings for the BBB.  For each part, the locations of the parts on the board are highlighted.

## 10KOhm Resistors



## 330Ohm Resistors



## 0.75 pF Caps



## 12 pF Caps



## 1 uF Caps



## 22 pF Caps



## Voltage Regulator



## Button



## Crystal



## LEDs



## Power Switch



## Balun



## Microcontroller



## FTDI Header



## SPI Header



## Battery Terminal



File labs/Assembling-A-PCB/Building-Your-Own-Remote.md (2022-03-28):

# Building Your Own Remote

The base model of the remote is what we have in class.  There are several options you can add.

## Electrical Components

You'll need to order the parts that are required for the remote but not for the breakout board.  To do so:

1.  Go to https://www.digikey.com/ordering/shoppingcart?lang=en
2.  Click `Upload a File` select [remote.digikey-bom.csv](boms/remote.digikey-bom.csv).
3.  Column B is the Digikey part number.  Column C is the quantity.  Ordering 1 spare of everything is not a bad idea. 
4.  Complete you order.

## Mechanical Components

Items with a "*" I can provide, since I buy them in bulk.

| Desc |  URL | Qty | 
|---|---|-----|
| FTDI cable |  https://www.adafruit.com/product/206 | 1 | 
| USB Micro cable  |  You probably have one of these | 1 |
| Display | https://www.sparkfun.com/products/14072 |  1  |
| LCD mount screws	1 1/4 in | 	https://www.mcmaster.com/90272a087 | 4 *| 
| Gimbal screws	1 1/2 in |	https://www.mcmaster.com/90272a088 | 8 *|
| Nuts for gimbals and PCB	|	https://www.mcmaster.com/90480a003 | 12 *| 
| Servo cable 	| https://www.amazon.com/gp/product/B01J81HQ9Y | 2 *|
| 3/8" spacer | https://www.mcmaster.com/94639a709 | 4 * |
| 1/2" spacer | https://www.mcmaster.com/94639a713 | 4 * |
| 1" spacer |  https://www.mcmaster.com/94639a667 | 8 * |
| Battery cable | https://www.alibaba.com/product-detail/Wholesales-explosion-proof-2-pin-Molex_60813679908.html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 | 1 *|
| Baseplate | na | 1 * |

## Gimbals

These are a little harder.  They are frequently out of stock.  They are also different than the ones on the remote I loaned you.  Unfortunately, those gimblas have been discontinuned.

| Desc | URL | Qty | 
|---|-----|-----|
|Gimbal (L) |https://hobbyking.com/en_us/turnigy-9x-9ch-transmitter-replacement-throttle-rudder-gimbal-1pc.html|	hobbyking|
|Gimbal (R) |https://hobbyking.com/en_us/turnigy-9x-9ch-transmitter-replacement-elevator-aileron-gimbal-1pc.html|	hobbyking|

## Assembling the Display

The remote includes a female header on the board that connects to a male header on the display.  Soldering the headers so they align is tricky, but there's a trick:

Barely insert the male header into the female header and the attach the display to the remote board using the screws.  You'll need 4 donuts between the LCD and the remote board.
 
Position the headers (without soldering them) so the male header connects to the display, and the female header connects to the remote.  Gently squeeze the two boards together and scew in place.

The headers are now perfectly positioned for soldering.  Solder them to the display and the board.

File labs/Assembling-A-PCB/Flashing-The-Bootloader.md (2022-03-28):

# Flashing the Bootloader and Bringing up Your Board

## You Will Need

1. Your board
2. A battery.
3. ISP Programmer
4. FTDI Board 
5. Multimeter
6. A computer with Arduino

## Electrical Short Test

By this time you should have received your PCB from manufacture and solder all the components to your board.  Before you power your board for the first time it is wise to check for shorts.  Use a multimeter to check for shorts between VBAT and GND and between 3.3V and GND.  Set the multimeter in continuity mode:
  
Continuity test

Then apply the probes to the test points on or breakout headers.  If you hear a beep when touching a power net and a ground net, there is a short somewhere in your board and you need to fix it.  Talk to the TA or the instructor.
    
## Sanity Check (Device Signature Verification)

The in-system programmer (ISP) let's us program the microcontroller while it is installed on a PCB.  The first step is to connect the ISP programmer to the board.  Here's picture of the programmer:

AVR ISP Board

Attach a charged battery to your board, then connect the board to the AVR ISP programmer and the USB cable to your computer.  The 6-pin connector attaches the 6-pin header on your board.  The cable should point toward the three dashed lines on the side of the header:

ISP polarity

If the lights on the programmer go out, you have an electrical problem.  Look for solder bridges, then talk to the course staff.

The next step is to establish communication between your board and the ISP programmer. 

ISP polarity

First, check if your compute can communicate with the board.  For this (and the rest of the flashing process) we are going to use a command line tool called `avrdude`.  It can do tons of things to microcontrollers and is what Arduino uses internally.

Open your command line and type the following (it can take a few seconds to run):

```
avrdude -c usbtiny -p atmega128rfa1
```

If this doesn't work, check the following

* The `avrdude.exe binary` is in `Arduino/hardware/tools/avr/bin` on Windows and in `/usr/local/bin/avrdude` in MacOS.
  - You can add this path to your environmental variables paths so you can use this command in any directory in your shell.
* `avrdude.exe` asks for a `avrdude.conf` file. This file may be located in   `Arduino/hardware/tools/avr/etc`
  - You can copy averdude.conf to `Arduino/hardware/tools/avr/bin` or you can add the path to where you dowloaded `averdude.conf` like in the following command: `avrdude -c usbtiny -p atmega128rfa1 -C ~/Downloads/avrdude.conf`
* If avrdude doesn’t recognize the "Pocket AVR Programmer" you can find the drivers in the following website: https://learn.adafruit.com/usbtinyisp/download.

When it's finally successful, you'll see a message like in the following image should be displayed.

AVRDude Success

If the command displays an error (see images below) it means that the computer is not able to communicate to your board or that your computer couldn’t find the AVR ISP Programmer.

AVRDude Error

The above error happens when your computer can’t find the AVR ISP Programmer. To solve this check that the device driver for the AVR ISP Programmer is installed.  If the tool suggests that your "override" with `-F`, don't bother.  It won't help.  Talk to the course staff.

For more information about how to use avrdude check this website: https://learn.sparkfun.com/tutorials/pocket-avr-programmer-hookup-guide 

## Flashing the bootloader

You are now ready to "flash" the bootloader.  This means we are going to write the bootloader into the non-volatile memory of the microcontroller.  The bootloader is a small program that allows us to reprogram the microcontroller over the serial port instead of the ISP header.
  
You’ll need the hex file that contains the bootloader.  It’s part of the `QuadClass_Atmega128RFA_Arduino_Addon` repo you intalled in Arduino during the first Arduino lab.  The file you need is `QuadClass_Atmega128RFA_Arduino_Addon/avr/bootloaders/ATmegaBOOT_atmega128rfa1.hex`

To flash the bootloader, run the following commands. The last one will fail, see below.

```
 cd <your quacopter repo>/firmware/hardware/QuadClass_Atmega128RFA_Arduino_Addon/avr/bootloaders/
 avrdude -p atmega128rfa1 -c usbtiny -e -u -U lfuse:w:0xff:m -U hfuse:w:0xda:m -Uefuse:w:0xf5:m lock:w:0x3F:m
 avrdude -p atmega128rfa1 -c usbtiny -B 1 -U flash:w:ATmegaBOOT_atmega128rfa1.hex -U lock:w:0x0f:m
```

The second command sets the fuses in the AVR microcontroller to configure the microcontroller to use an external clock, among other things.  The third command copies the `ATmegaBOOT_atmega128rfa1.hex` to the microcontroller.

The last command will fail due to a big in `avrdude`. You’ll see something like this:

AVRDude Spurious Error

This is a known issue and is because the `USBTinyISP` protocol that we are using with the “[Pocket AVR Programmer](https://www.google.com/url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)" is incapable of addressing memory addresses in excess of 64 KB. In our case the atmega128RFA1 is of 128K.
“… Someone in the code put uint_16 for the address so it overflows…” (Ignore the error!)

## Programming The Board With Arduino

Open up the Arduino IDE and make sure it's configured properly (See notes in "Programmin The Hardware Lab").  The run the blink test on the board.  Your PCB should have a blinking light!  

Your board is not ready for use!

## Bringup

"Bringing up" a board means carefully checking that each component of the board works as expected.

There is a tendency to move to quickly during bringup, but take your time.  If you try to run a big piece of software at first, the bugs will be much harder to find.

### Bringing up the BBB

You should be able to the Arduino blinking light test.  You can also run `test_remote_harness.ino` on the BBB and `test_remote.ino` on your loaner remote.

### Bringing up the Remote

A purpose-built tester is useful here.  For instance, for the remote, there is `Quadcopter-Remote/src/test_remote/test_remote.ino` and `Quadcopter-Remote/src/test_remote/test_remote_harness.ino`.  `test_remote.ino` runs on the remote and transmits a bunch of data to another device (a working remote or a FCB) running `test_remote_harness.ino`.  It tests all the software-accessible components of the remote.
It doesn't, however, check that the battery charger works.  So, you'll need to verify that mannually.

### Bringing up Your Quadcopter

Your code from the first remote/FCB can also serve as a good starting point.  When bringing up your quadcopter, remember that the pin assignments may be differnt, so you may need to modify the code slightly.

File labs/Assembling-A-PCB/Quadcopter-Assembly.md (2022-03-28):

# Assembling Your Quadcopter

Assembling your quadcopter is similar to assembling the BBB board, but more involved because there are more components.

You should re-read the [BBB assembly lab](Readme.md).  Everything there applies here as well, including the suggested order for assembly.  Below are just the differences.

If you want to build a remote to keep, here are [the instructions](Building-Your-Own-Remote.md).

## Preparing Your Part Kit

You can think of the part kit for your quadcopter as breaking into three parts:

1.  The parts that are common to all the quadcopter designs.
2.  Additional instances of the parts common parts.
3.  Parts specific to your design.

For the first group, we have part packets prepared for you just as we did with the BBB board.  Grab *one* of each packet.

The second group is usually resistors and mosfets (e.g., to control LEDs).  Take additional packets of these parts to get what you need.

For the third group, we have ordered parts from Digikey for you.  Each part will come in it's own bag with the "customer reference" field containing the list of reference designators that the parts correspond to.

## Part Notes

The quadcopters have a few parts that were not on the BBB.  Here they are (quantities are for the core design.  You may have other parts, depending on your LED design):

### Surface Mounts Parts

| Part | Qty | Picture |
|---|-----|---|

| MOSFET            | 4   |   Mosfet.                    |
| IMU               | 1.  | IMU.                            | 
| 10KOhm Resistors  | 6   | Resistor.                 |
| 330Ohm Resistors. | 2.  ||
| 220 uF Capacitor  | 5   |   Caps          |
| 0.01uF Capacitor  | 1   | Capacitors.              |
| 0.1uF Capacitor.  | 4   ||
| 10uF Capacitor.  | 1   ||
| 12uF Capacitor.  | 2   ||
| 22uF Capacitor.  | 1   ||
| 0.75uF Capacitor.  | 1   ||
| Diode             | 4   | Diode.            | 
| MCU.              | 1   | MCU.                  |
| Crystal           | 1   | Crystal.                      |
| Balun             | 1   | Balun.            |
| LED Red &Green    | 1   | LED.                |
| Voltage Regulator | 1   | Vgg.            |

### Through Hole Parts

| Part | Qty | Picture |
|---|-----|---|
| Motor Sockets | 4 | Motor Socket. |
| FTDI Header. | 1 | FTDI. |
| Button | 1 | Button. |
| Screw Terminals | 1 | Screw. |
| 2-pin Header | 3 | header. |

## Assembly Drawings

Eagle provides a simple mechanisms to help you place parts.  Open your `.brd` file.  You need to enable  the "Design Manager" (`View->Design Manager`).

The "Devices" pane shows a list of all the parts in your design.  Sort the list by "value" and hide the other columns (wrench icon).

You can now select all the parts of a given type and Eagle will highlight their location on the board.

## Time Management

Assembling your boards will take longer than the BBB, because there are more parts, and class time is limited.  To ensure you have time to apply paste, place parts, and reflow the boards, you must start applying paste **at the beginning of class**.  

We will have stations set up for applying paste at 10am on days we are doing assembly for this purpose.

This means you need to have your part kit completely assembled **the class period before**.  If your part kit is not ready at the starte of class, we will not let you start assembly that day.

You also need to work quickly.  Your quadcopters have between 70 and 100 parts (vs 30 for the BBB), and you need to complete assembly at least 1 hour before the end of class (2pm).  This means you need to be placing 1 part ever 30-45 seconds or so.  Keep an eye on the clock.

## Scheduling

On assembly days, the TA will set have parts out by 10am and paste assembly stations ready by 10:30.

On Tuesdays, you must have boards ready for reflow by 1pm. 

On Thursdays, we have to vacate the room by 1pm.  I would suggest starting (and finishing) assembly in the main maker space work area.  Again, you must be ready to reflow by 1pm.

The TA and I both have other obligations after class after on some days.  This means that if you aren't ready to reflow in time, we may not be able to stay after to reflow your board.

The soldering stations are available for hand-soldering the through-hole parts.  You can work on this whenever the maker studio is open.

## Tips, Tricks, Bells, and Whistles

### Attaching the Motors

The spec for the board, should provide a snug fit for your motors, but the board milling process is not perfectly precise.  Also, the motors are subject to significant stress during testing (as your board bangs around the test stand).  To hold the motors in place, hot glue works well.  Position the motors as you like and apply 1-2 _small_ amount of got glue to the corner formed between your PCB and the motor.   You don't need very much and applying alot will make a mess and make it difficult to remove the motors later.

Do not using anything stronger (e.g., super glue or gorilla glue).  It makes a mess, is too brittle, and is very hard to remove.  Hot glue is really the about perfect.

### "Feet" for Your Quadcopter

It's useful to have something for your quadcopter to stand on so it sits level on the ground.  This is especially handy when you are calibrating your IMU.   You have several options:

1.  You can use the motors.  Position them to ride low, so the bottom extends down a ways, and make sure you put them all at the same height.  The draw back is that wires can get banged around.
2.  3D print something.   Go crazy, but remember that weight is an issue.
3.  A piece of light foam would make a pretty good landing pad.  You can even use part of a household sponge.
4.  The battery can also help here if you mount it underneath.

### Attaching the Battery

The battery is awkward, and it's a hard problem to solve.  Many things can work, but few look great:  Blue tape, rubber bands, velcro.  

One thing that might help is shortening the wiring harness that connects to your quadcopter.  Play around until you find a good length and then trim it short.

We also have some plastic "cages" you're welcome to use.

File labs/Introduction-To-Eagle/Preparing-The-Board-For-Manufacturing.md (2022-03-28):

# Part 3: Preparing the Board for Manufacturing

Once the design is finished, we need to translate it a format that the manufacturer can understand.

## Generating the CAM files
In order to have a board manufactured an Eagle or Fusion360 file is not sufficient. Instead, you need to produce a set of computer aided manufacturing (CAM) files for the design. Fusion360 provides a tool called the "CAM processor" to generate these files for your design. CAM files are also called "Gerber files."

Different board manufacturers (i.e., "board houses") require different types of CAM files and some require different CAM setups for different levels of board complexity. We will be using https://www.pcbcart.com/, a Chinese manufacturer that is pretty reliable and fast. Each board house and service level has different sets of restrictions the design must meet and, potentially, a different set of design files they require. Two files define how Fusion360 interacts with the board manufacturing process.

The first is the .cam file. This defines the set of gerber files we will send to the manufacturer. The second in the .dru file that defines the design rules for the board house. The specs for JLCPCB's PCBs are here: https://www.pcbcart.com/pcb-fab/standard-pcb.html. Fusion360 uses the design file to, for instance, guide the autorouter and perform sanity checks on our design.

The DRU and CAM files you need for this lab are in `Eagle/CAM/pcbcart-4layer.cam` and `Eagle/CAM/pcbcart-4layer.cam`.

<!--
To select the CAM file you will use, select "Window->Control Panel" Then select "File->Open->Cam Job..." and navigate to Eagle/CAM/jlcpcb-2layer-eagle9.cam.
You should see a window like this:
![](images/cam1.png)
Leave this window open and return to the board editor window. 
-->
To select the CAM file, return to the board editor window, navigate to the `Manufacturing` tab and select the `CAM Processor`:



A window will appear like this:
<!--
the same window will reappear but with some additional information filled in:
-->


Then click on the "load job -> Open Cam File". This will allow you to select the required CAM file. 


The tabs on the left correspond to the CAM files that the CAM processor will generate for this design. The body of the window contains configuration parameters for each of the CAM files. Don't touch any of these settings.

Click "Process Job". A progress bar will appear briefly and then vanish. The CAM files have been generated, and are saved wherever you specified.

## Viewing the CAM files
Fusion360 cannot open or view CAM/Gerber files. For that you need a Gerber viewer:

* Mac: I like Cuprum: http://www.wortum.com/cuprum/.
* Windows: http://www.viewplot.com/ or https://www.pentalogix.com/t/software-products/viewmate.
* Linux: http://gerbv.geda-project.org/ (It might already be installed. Or do `sudo apt-get install gerbv`)

The instructions below are for the Cuprum viewer on a Mac.

Launch Cuprum and create a new project (Command-N). Click "Import..." and then select all the files generated by the CAM file generator. These are:

* `throughhole.cmp`: This is the copper on the top layer of the board. You should see metal traces corresponding to the routed traces you added in Eagle. You should also see a circle at each pad.
* `throughhole.stc`: This is the solder mask for the top of the board. Solder mask is the green material that covers the surface of the board. It protects the metal from corrosion and accidental electrical connections. This layer is a negative. It shows holes that will appear in the solder mask, exposing the parts of the copper that we need to make connections to. There should be a circle around each of the pads.
* `throughhole.plc`: The silkscreen layer contains the write documentation and markings that appear on the surface of the board. It should contain the outlines of the parts and their reference designators (e.g., "LED1").
* `throughhole.sol:` Bottom metal layer.
* `throughhole.sts`: Just like `stc`, but for the bottom of the board.
* `throughhole.pls`: Just like `plc', but for the bottom of the board.
* `throughhole.ncd`: This is the drill file. It determines where holes will be drilled in the board. There is one hole for each of the pads in our design. There would also be pads for Vias and “mechanical holes” for mounting etc. Unfortunately, the format the Seeed requires for the drill file does not display well in the gerber viewer, so the holes will be all over the place.

Load them, and then examine each by toggling its visibility in the viewer:



3. Make sure the File name matches the File Content. You will probably need to change the File Content for the *.drd to *NC Drill.*

After you've verified that the CAM files look good, you're ready for [part 4](Creating-Surface-Mount-Parts.md)!

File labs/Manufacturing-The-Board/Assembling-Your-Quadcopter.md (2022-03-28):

# Part 2: Quadcopter HW debugging and Motors rotation

## 

## Debugging your quadcopter hardware
Before moving to MultiWii is highly recommendable to test the hardware in your quadcopter and see if everything works.

* *Testing IMU:*

    * Some of your designs have the low-order bit of the IMU I2C address set incorrectly. You can change the values the library uses by changing `LSM9DS1_ADDRESS_ACCELGYRO` in `Adafruit_LSM9DS1.h`. For some of you the IMU seems to be reporting the wrong ID as well. You can disable this check in `Adafruit_LSM9DS1.cpp` look for `LSM9DS1_XG_ID`. You’ll probably need to disable the check on `LSM9DS1_MAG_ID` too.

* *Testing Antenna:*
* You can use the code you did for Lab1 or you can move on to Multiwii, install the code and test it with the controller.
* *Testing LEDs:*

    * Make a code for turning on and off the LEDS.

* *Testing* *Motors:*

    * Make a code for testing the motors.

Just for the reference here are the pinouts of the ATmega128RFA1 chip and the numbers in Arduino.

[image:https://lh3.googleusercontent.com/Y-g-L73snOodRgEldgMqoe6ZkE8HG2E9gaV6Dzdi6jYx83d-sB-QP6XNzDjoGwq-7iR392esXOIleYe5_OIb4UZCEGeV_r1Y0PgZhrV2A9kyVv5TjLU=w371]

## 

## Connecting the Motors
The proper way of connecting is the following:

[image:https://lh6.googleusercontent.com/Udl2DeEpNyP6dQ8fEz-RLj-oiEe32Y_gbZe2rgo36ftyuY-uYHG6NjrNH1-W-WyVhS_R_edBquHyBHo3qT8ogQRrjCrvrM5WJWKGY6VzKYvwgfqC9HY=w673]

Depending on your Quadcopter configuration (Quad + or Quad X) connect the motors so that the above picture match.

Check your schematic to figure out which pin of the connector is the positive and which one is negative.

[image:https://lh6.googleusercontent.com/5aGaMqNbBq0CTBH3FEu3-_WgT2El_n9up7iqOvvy34DylCeBS4ww7qkAEeE8xfh9YAnAo2nQiIxwplMkVLGj-BiH08DTkNwuzSFGxCnuPnhBGH9O2TY=w170]

If you switch the polarity of the cables your motor is going to spin in the opposite direction and contrary to the brush inside the motor therefore reducing the life of the motor. That is why there exists two types of motors (CW and CCW).

## 

## Propellers
There are two types of propellers (CW and CCW). When inserting the propellers to the motors just make sure that the motors trow air to down and not up. Also propellers can come in different colors, is common to place different colors at the front and back of your quadcopter to know the orientation when it is flying.

[image:https://lh4.googleusercontent.com/m_oq1LI_hATVSxeVcqnpruCNJ5CESinBkgc32T9WAJ6Aa5gUfhQjtpXtC_OJOs0j954Ys0B-ZLXjJV_FZHb7IjceEdLDrKEXaQAISViopxvt4Z-G0Hg=w673]

# Part 3: Flight Control

## 

## Tasks to Perform (Part Lab06c): Flight Control Features
### 

### Implement Control Features
You need to implement the following features in your quadcopter firmware

Arm

When you power up your quadcopter it should be “disarmed.” This means that it will not respond to the remote. This is safety feature (to prevent the props from running unexpectedly) and an opportunity to calibrate your sensors.

A common way to arm a quadcopter is to hold the throttle at zero and the roll gimbal all the way to one side or the other and wait a few seconds. You can use whatever method you like, but it must include the throttle being at zero.

It’d be nice to indicate when the quad is armed by flashing a light or something.

Calibrate your IMU

When the quadcopter boots, it should calibrate the IMU. You should assume that the quadcopter is sitting on something level and check the measurements from the IMU to account for any offsets. Your quadcopter should refuse to arm itself until it’s calibrated.

It’d be nice to have a light that shows when it’s calibrating and/or when it’s ready to be armed.

## 

## Complete The Flight Controller
The code you wrote for the test stand should be more or less ready to run on your quadcopter. In theory, the only changes you should need to make to get flying (but maybe not steering) are to update the pin assignments for your motors, re-tune the PID values, and add a PID channel for roll (assuming you were working on pitch on the test stand). For full flight control you’ll need to add a PID channel for and yaw.

### 

### Tuning the PID Values
The process is same as it was for the test stand, with a few small changes.

1. Your quadcopter probably has more power than your test stand because the power delivery system is cleaner (your nice big power/ground planes are much better than the skinny wires on the test stand)
2. The mass and balance of your quadcopter is different than the test stand.
Both of these mean that the correct PID values for your quad are probably different than those for the test stand.

You can tune the values by attaching your quadcopter to the test stand. To do this, you can pull the pivot platform off the axel and attach your quad using tape or zip ties (available in the maker studio).

### 

### Adding the Roll PID Channel
The PID control for roll works the same as for pitch. In theory, if your quad is symmetric the PID values should be the same too. I would check by rotating the quad on the test stand and seeing how stable it is.

Once you have the roll channel added, your quadcopter should be able to fly — i.e., you should be able to increase the throttle and it should leave the ground and fly level. However, it may spin because you don’t have yaw control yet.

For your quad’s safety, you may want to attach the prop-guards that came in your crash kit. The prop-guards make it less likely that the props will cut someone and they also help prevent damage to the motor shafts — a hard crash on a prop can bend the shaft and ruin one of your motors.

These are the loopy piece of black plastic. It has four mounting points that attach the motors, but the dimensions won’t quite match your quad. You can cut it into four pieces and attach a piece to each motor.

### 

### Adding the Yaw PID Channel
The Yaw channel is a little different. Use the left-right axis of the left controller gimbal to set the rate of rotation. This is exactly what the gyro gives you. The gyro is also pretty low noise, so you probably won’t need to do much filtering.

Tuning this PID loop is harder, since the test stand doesn’t spin. However, yaw is also not as critical for stable flight so you can probably tune it while the quadcopter is in the air.

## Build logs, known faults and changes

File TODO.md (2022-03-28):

# TODO

1.  Remove depndency on SoftwareSerial2

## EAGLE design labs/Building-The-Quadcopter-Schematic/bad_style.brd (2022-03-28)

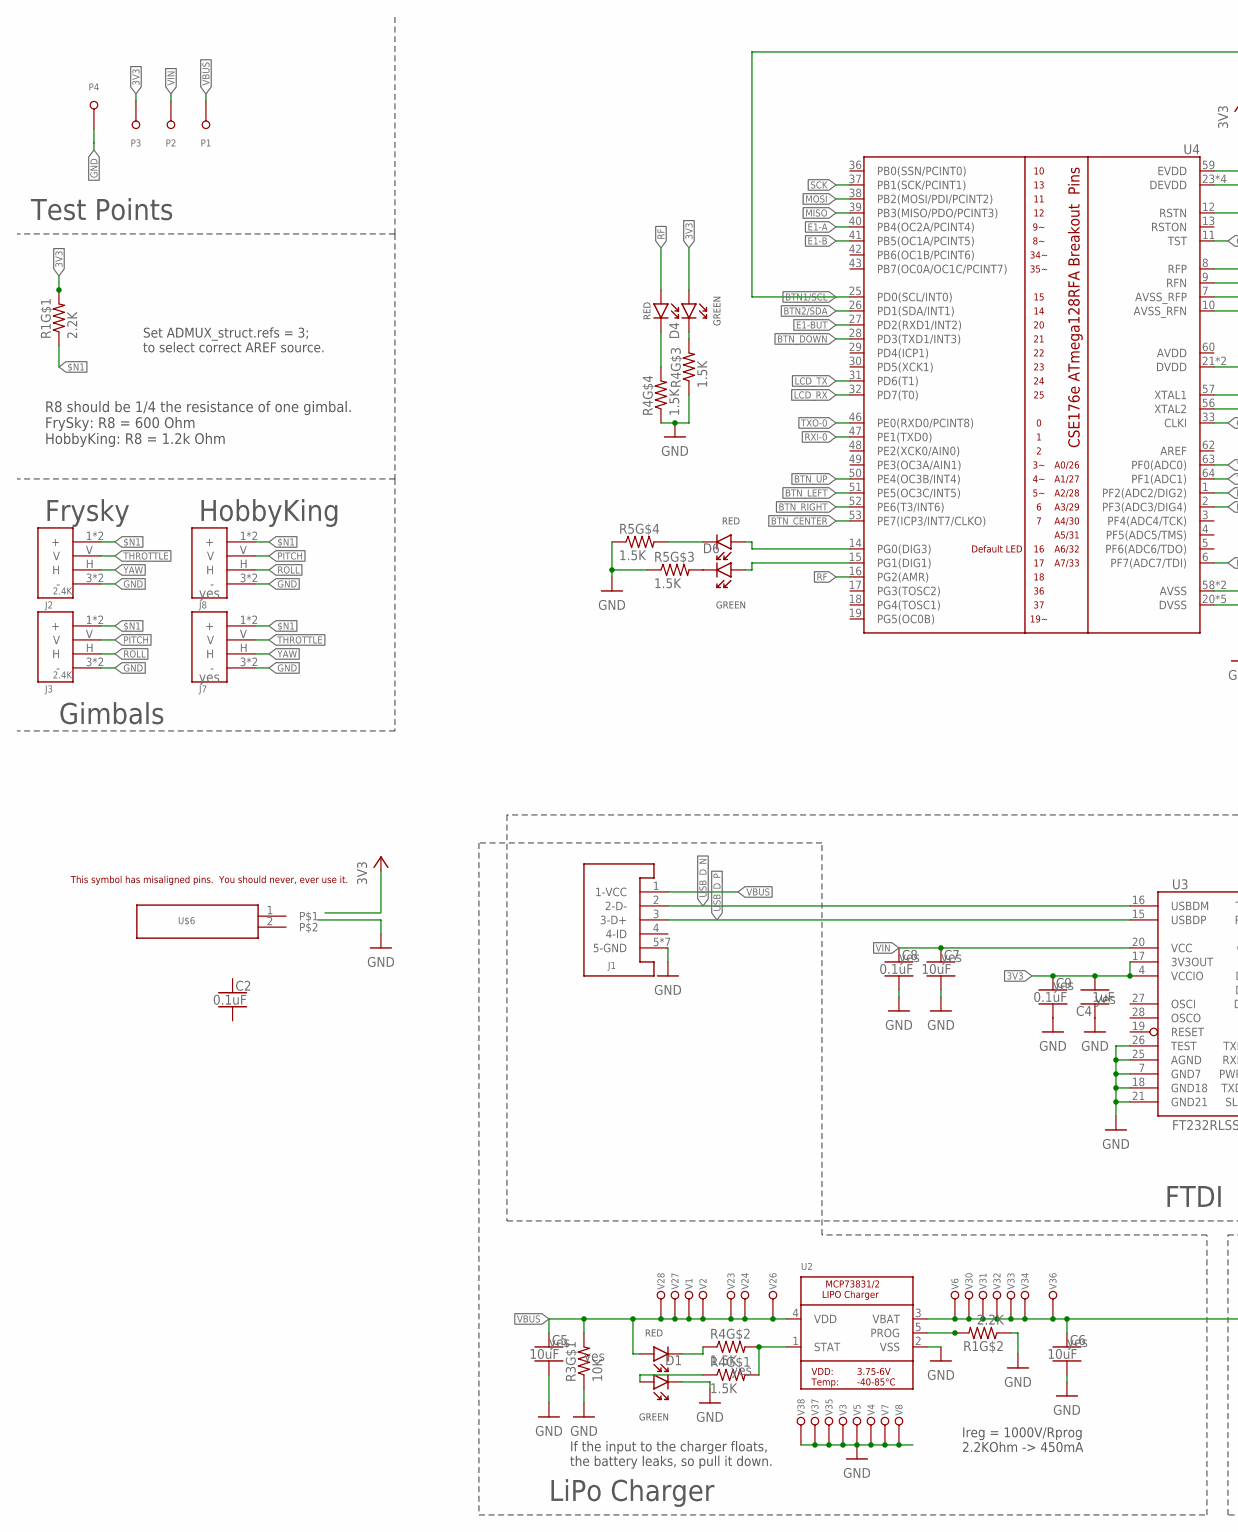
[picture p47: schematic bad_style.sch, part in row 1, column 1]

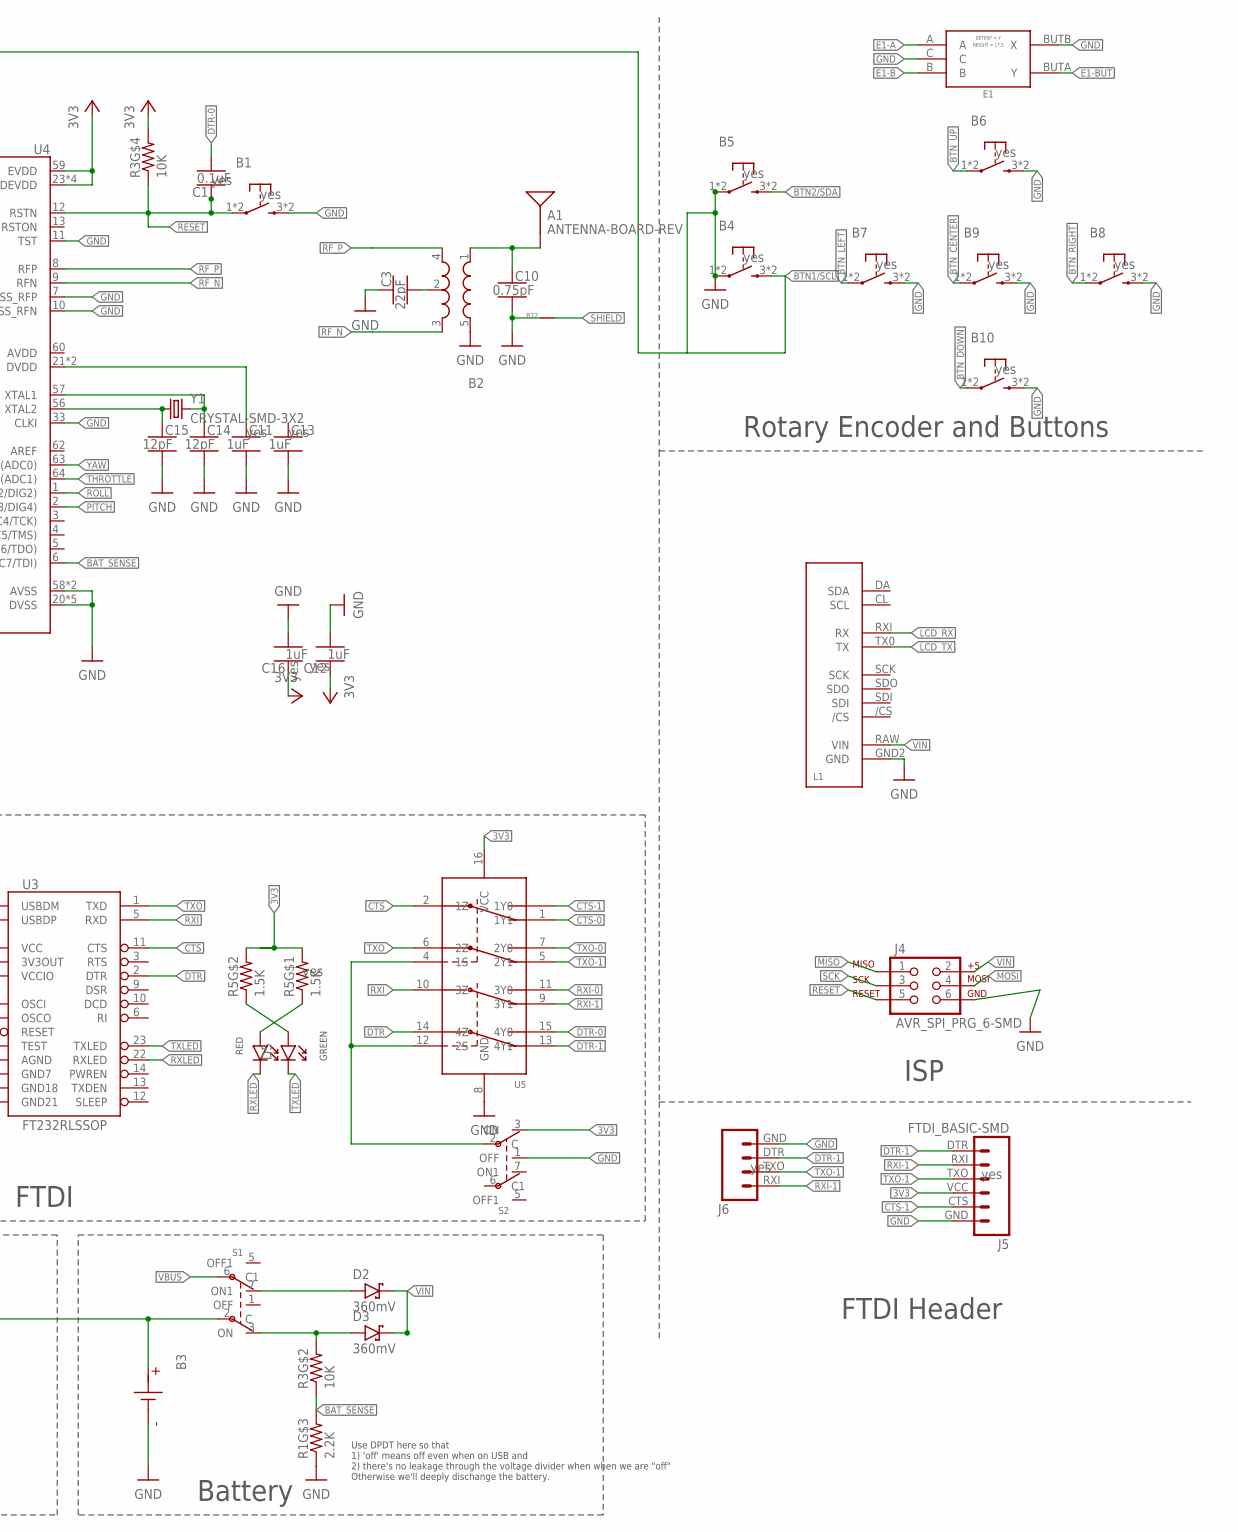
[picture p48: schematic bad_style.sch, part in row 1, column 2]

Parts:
A1: ANTENNA-BOARD-REV; ANT_PCB_2.4GHZ_NRF8001_1.6MM_1OZ_REV
B1, B4, B5, B6, B7, B8, B9, B10: PUSHBUTTON_-4.5X4.5; 4.5MM_TACTILE_SWITCH_TL3305AF160QG
B2: BALUN0805; BALUN
B3: BATTERY-SMD; MOLEX-BATTERY-CONNECTOR-SMD-51005-2P
B12: NET_BRIDGE
C1, C2, C8, C9: 0.1uF; CAPC1608X100
C3: 22pF; CAPC1608X100
C4, C11, C12, C13, C16: 1uF; CAPC1608X100
C5, C6, C7: 10uF; CAPC1608X100
C10: 0.75pF; CAPC1608X100
C14, C15: 12pF; CAPC1608X100
D1, D4, D5, D6: LED-2X-GREEN/RED-1.6X1.5MM; LED-2X-LITE-ON-1.6MMX1.5MM
D2, D3: 360mV; SODFL3516X96
E1: ROTARY-ENCODER-W/BUTTON-BOURNS-PEC12R-4217F; BOURNS-PEC12R
J1: USB-MICROA-AMPHENOL-10118192-0001LF; USB-MICROA-10118192-0001LF
J2, J3: 2.4K; JST-13-PTH
J4: AVR_SPI_PRG_6-SMD; 2X3-SMD
J5: FTDI_BASIC-SMD; FTDI-BASIC-SMD
J6: FTDI-4PIN-RIGHT-ANGLE-SMD; HEADER-2X2-0.1IN-MALE-RIGHT-ANGLE-SMD
J7, J8: FRSKY-GIMBAL-2X-SERVO-SMD; 2X-SERVO-SMD
L1: SPARKFUN_SERLCD_SERIAL_REDUCED-SMD; SPARKFUN_SERLCD_16X2_REDUCED_SMD
P1, P2, P3, P4: TEST-POINT; TEST-POINT-KEYSTONE-5000
R1: 2.2K; RESCAXS50P200X100X45-8
R3: 10K; RESCAXS50P200X100X45-8
R4, R5: 1.5K; RESCAXS50P200X100X45-8
S1, S2: SWITCH-DPDT-300MA-6V-SMD; JS202011JCQN
U2: MCP73831T-2ACI/OT; SOT23-5
U3: FT232RLSSOP; SSOP28DB
U4: ATMEGA128RFA1; QFN-64
U5: DPDT-X2; SOP65P640X110-16
U$6: DONT_USE; SCREW-TERMINAL-1X2-2.54MM
V1, V2, V3, V4, V5, V6, V7, V8, V23, V24, V26, V27, V28, V30, V31, V32, V33, V34, V35, V36, V37, V38: LOCKED-VIA-0.2; VIA-0.2MM
Y1: CRYSTAL-SMD-3X2; OSCCC320X250X85

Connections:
3V3: C4.2, C9.1, C12.1, C16.1, D4.A1, J5.VCC (4), P3.T, R1.5 (2), R3.8 (2), R5.5 (2), R5.6 (2), S2.3 (ON), U3.4 (VCCIO), U3.17 (3V3OUT), U4.23 (DEVDD), U4.34 (DEVDD), U4.44 (DEVDD), U4.54 (DEVDD), U4.59 (EVDD), U5.16 (VCC)
$N1: J2.1 (+), J2.4 (+), J3.1 (+), J3.4 (+), J7.1 (+), J7.4 (+), J8.1 (+), J8.4 (+), R1.4 (1)
ANTENNA: A1.FEED, B2.1 (IN), C10.1
BAT_SENSE: R1.7 (2), R3.3 (1), U4.6 (PF7(ADC7/TDI))
BCAP: B2.2 (GND), C3.2
BPOS: B3.P, C6.1, S1.2 (C), U2.3 (VBAT), V6.P1, V30.P1, V31.P1, V32.P1, V33.P1, V34.P1, V36.P1
BTN1/SCL: B4.3 (2), B4.4 (2), U4.25 (PD0(SCL/INT0))
BTN2/SDA: B5.3 (2), B5.4 (2), U4.26 (PD1(SDA/INT1))
BTN_CENTER: B9.1, B9.2 (1), U4.53 (PE7(ICP3/INT7/CLKO))
BTN_DOWN: B10.1, B10.2 (1), U4.28 (PD3(TXD1/INT3))
BTN_LEFT: B7.1, B7.2 (1), U4.51 (PE5(OC3C/INT5))
BTN_RIGHT: B8.1, B8.2 (1), U4.52 (PE6(T3/INT6))
BTN_UP: B6.1, B6.2 (1), U4.50 (PE4(OC3B/INT4))
CLK_NEG: C15.1, U4.56 (XTAL2), Y1.1
CLK_POS: C14.1, U4.57 (XTAL1), Y1.3 (2)
CTS: U3.11 (CTS), U5.2 (1Z)
CTS-0: U5.3 (1Y0)
CTS-1: J5.CTS (5), U5.1 (1Y1)
DTR: U3.2 (DTR), U5.14 (4Z)
DTR-0: C1.2, U5.15 (4Y0)
DTR-1: J5.DTR (1), J6.DTR (3), U5.13 (4Y1)
E1-A: E1.A, U4.40 (PB4(OC2A/PCINT4))
E1-B: E1.B, U4.41 (PB5(OC1A/PCINT5))
E1-BUT: E1.BUTA (Y), U4.27 (PD2(RXD1/INT2))
GND: B1.3 (2), B1.4 (2), B2.5 (GND), B3.G (N), B3.G2 (N), B3.G3 (N), B4.1, B4.2 (1), B5.1, B5.2 (1), B6.3 (2), B6.4 (2), B7.3 (2), B7.4 (2), B8.3 (2), B8.4 (2), B9.3 (2), B9.4 (2), B10.3 (2), B10.4 (2), B12.P1, C3.1, C4.1, C5.2, C6.2, C7.2, C8.2, C9.2, C10.2, C11.2, C12.2, C13.2, C14.2, C15.2, C16.2, D1.C1, E1.BUTB (X), E1.C, J1.5 (5-GND), J1.6 (5-GND), J1.7 (5-GND), J1.8 (5-GND), J1.9 (5-GND), J1.10 (5-GND), J1.11 (5-GND), J2.3 (-), J2.6 (-), J3.3 (-), J3.6 (-), J4.6, J5.GND (6), J6.GND (4), J7.3 (-), J7.6 (-), J8.3 (-), J8.6 (-), L1.GND2 (GND), P4.T, R1.2 (1), R1.3 (1), R3.4 (1), R4.1, R4.2 (1), R5.1, R5.2 (1), S2.1 (OFF), U2.2 (VSS), U3.7 (GND7), U3.18 (GND18), U3.21 (GND21), U3.25 (AGND), U3.26 (TEST), U4.7 (AVSS_RFP), U4.10 (AVSS_RFN), U4.11 (TST), U4.20 (DVSS), U4.24 (DVSS), U4.33 (CLKI), U4.35 (DVSS), U4.45 (DVSS), U4.55 (DVSS), U4.58 (AVSS), U4.61 (AVSS), U5.8 (GND), V3.P1, V4.P1, V5.P1, V7.P1, V8.P1, V35.P1, V37.P1, V38.P1
LCD_RX: L1.RXI (RX), U4.32 (PD7(T0))
LCD_TX: L1.TX0 (TX), U4.31 (PD6(T1))
MISO: J4.1, U4.39 (PB3(MISO/PDO/PCINT3))
MOSI: J4.4, U4.38 (PB2(MOSI/PDI/PCINT2))
unnamed: D1.A1, R4.4 (1)
unnamed: D1.C2, R4.3 (1)
unnamed: D5.A1, R5.3 (1)
unnamed: D6.C2, R5.8 (2)
unnamed: D6.C1, R5.7 (2)
unnamed: D4.C1, R4.7 (2)
unnamed: D5.A2, R5.4 (1)
unnamed: D6.A2, U4.14 (PG0(DIG3))
unnamed: D6.A1, U4.15 (PG1(DIG1))
unnamed: R4.5 (2), R4.6 (2), U2.1 (STAT)
unnamed: R1.6 (2), U2.5 (PROG)
unnamed: D4.C2, R4.8 (2)
unnamed: D2.2 (A), S1.7 (ON1)
unnamed: C11.1, U4.21 (DVDD), U4.22 (DVDD)
PITCH: J3.V, J8.V, U4.2 (PF3(ADC3/DIG4))
PROG_SEL: S2.2 (C), U5.4 (1S), U5.12 (2S)
RESET: B1.1, B1.2 (1), C1.1, J4.5, R3.1, U4.12 (RSTN)
RF: D4.A2, U4.16 (PG2(AMR))
RF_N: B2.3 (OUT2), U4.9 (RFN)
RF_P: B2.4 (OUT1), U4.8 (RFP)
ROLL: J3.H, J8.H, U4.1 (PF2(ADC2/DIG2))
RXI: U3.5 (RXD), U5.10 (3Z)
RXI-0: U4.47 (PE1(TXD0)), U5.11 (3Y0)
RXI-1: J5.RXI (2), J6.RXI (1), U5.9 (3Y1)
RXLED: D5.C2, U3.22 (RXLED)
SCK: J4.3, U4.37 (PB1(SCK/PCINT1))
SHIELD: B12.P2
THROTTLE: J2.V, J7.V, U4.64 (PF1(ADC1))
TXLED: D5.C1, U3.23 (TXLED)
TXO: U3.1 (TXD), U5.6 (2Z)
TXO-0: U4.46 (PE0(RXD0/PCINT8)), U5.7 (2Y0)
TXO-1: J5.TXO (3), J6.TXO (2), U5.5 (2Y1)
USB_D_N: J1.2 (2-D-), U3.16 (USBDM)
USB_D_P: J1.3 (3-D+), U3.15 (USBDP)
VBAT: D3.2 (A), R3.6 (2), S1.3 (ON)
VBUS: C5.1, D1.A2, J1.1 (1-VCC), P1.T, R3.5 (2), S1.6 (C1), U2.4 (VDD), V1.P1, V2.P1, V23.P1, V24.P1, V26.P1, V27.P1, V28.P1
VIN: C7.1, C8.1, D2.1 (C), D3.1 (C), J4.2, L1.RAW (VIN), P2.T, U3.20 (VCC)
YAW: J2.H, J7.H, U4.63 (PF0(ADC0))

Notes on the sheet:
Ireg = 1000V/Rprog 2.2KOhm -> 450mA
LiPo Charger
Test Points
Frysky
HobbyKing
Rotary Encoder and Buttons
Battery
ISP
FTDI Header
Set ADMUX_struct.refs = 3; to select correct AREF source.
Gimbals
R8 should be 1/4 the resistance of one gimbal. FrySky: R8 = 600 Ohm HobbyKing: R8 = 1.2k Ohm
If the input to the charger floats, the battery leaks, so pull it down.
FTDI
Use DPDT here so that 1) 'off' means off even when on USB and 2) there's no leakage through the voltage divider when when we are "off" Otherwise we'll deeply dischange the battery.

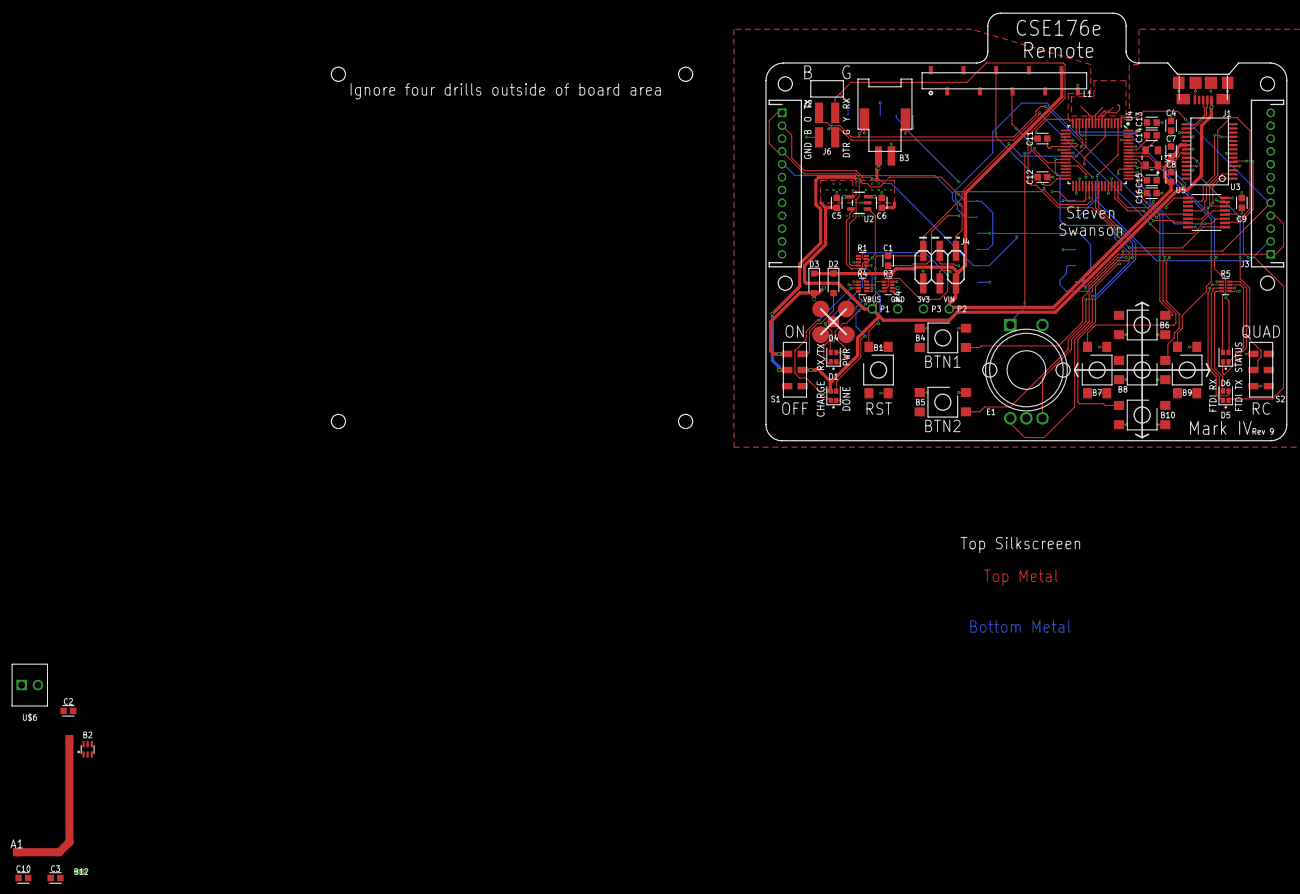
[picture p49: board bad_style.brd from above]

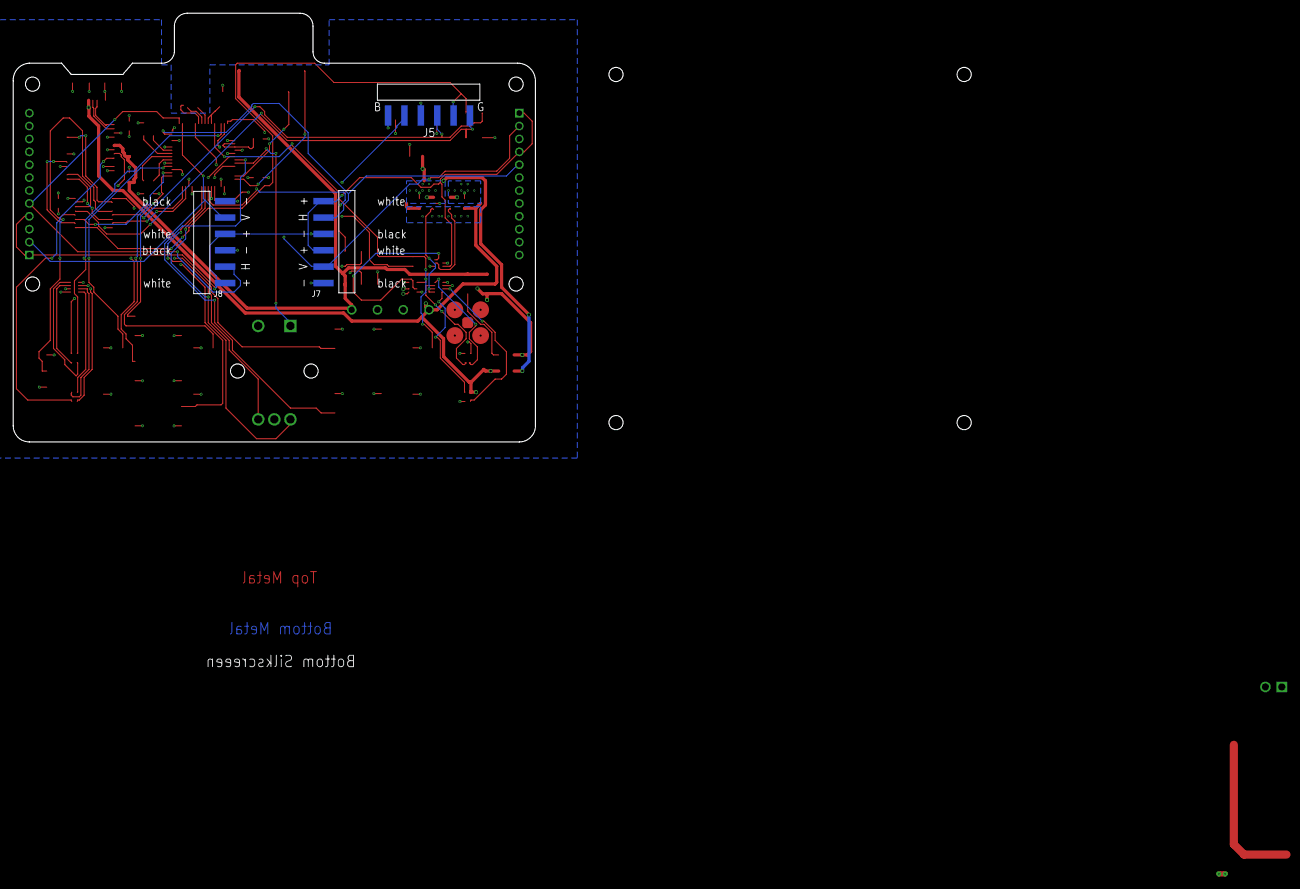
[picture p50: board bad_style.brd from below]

Board: 4 copper layers, 81.0 x 66.5 mm, 89 parts (3 on the bottom side), 65 nets.

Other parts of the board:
E$1, E$2: FRSKY-TARANIS-GIMBAL
U$1: 700MAH-BATTERY
U$2: QUADCLASS_LOGO_SMALL
U$3: LAYER_LABELS
U$4: 375MAH-BATTERY
U$5: 600MAH-BATTERY

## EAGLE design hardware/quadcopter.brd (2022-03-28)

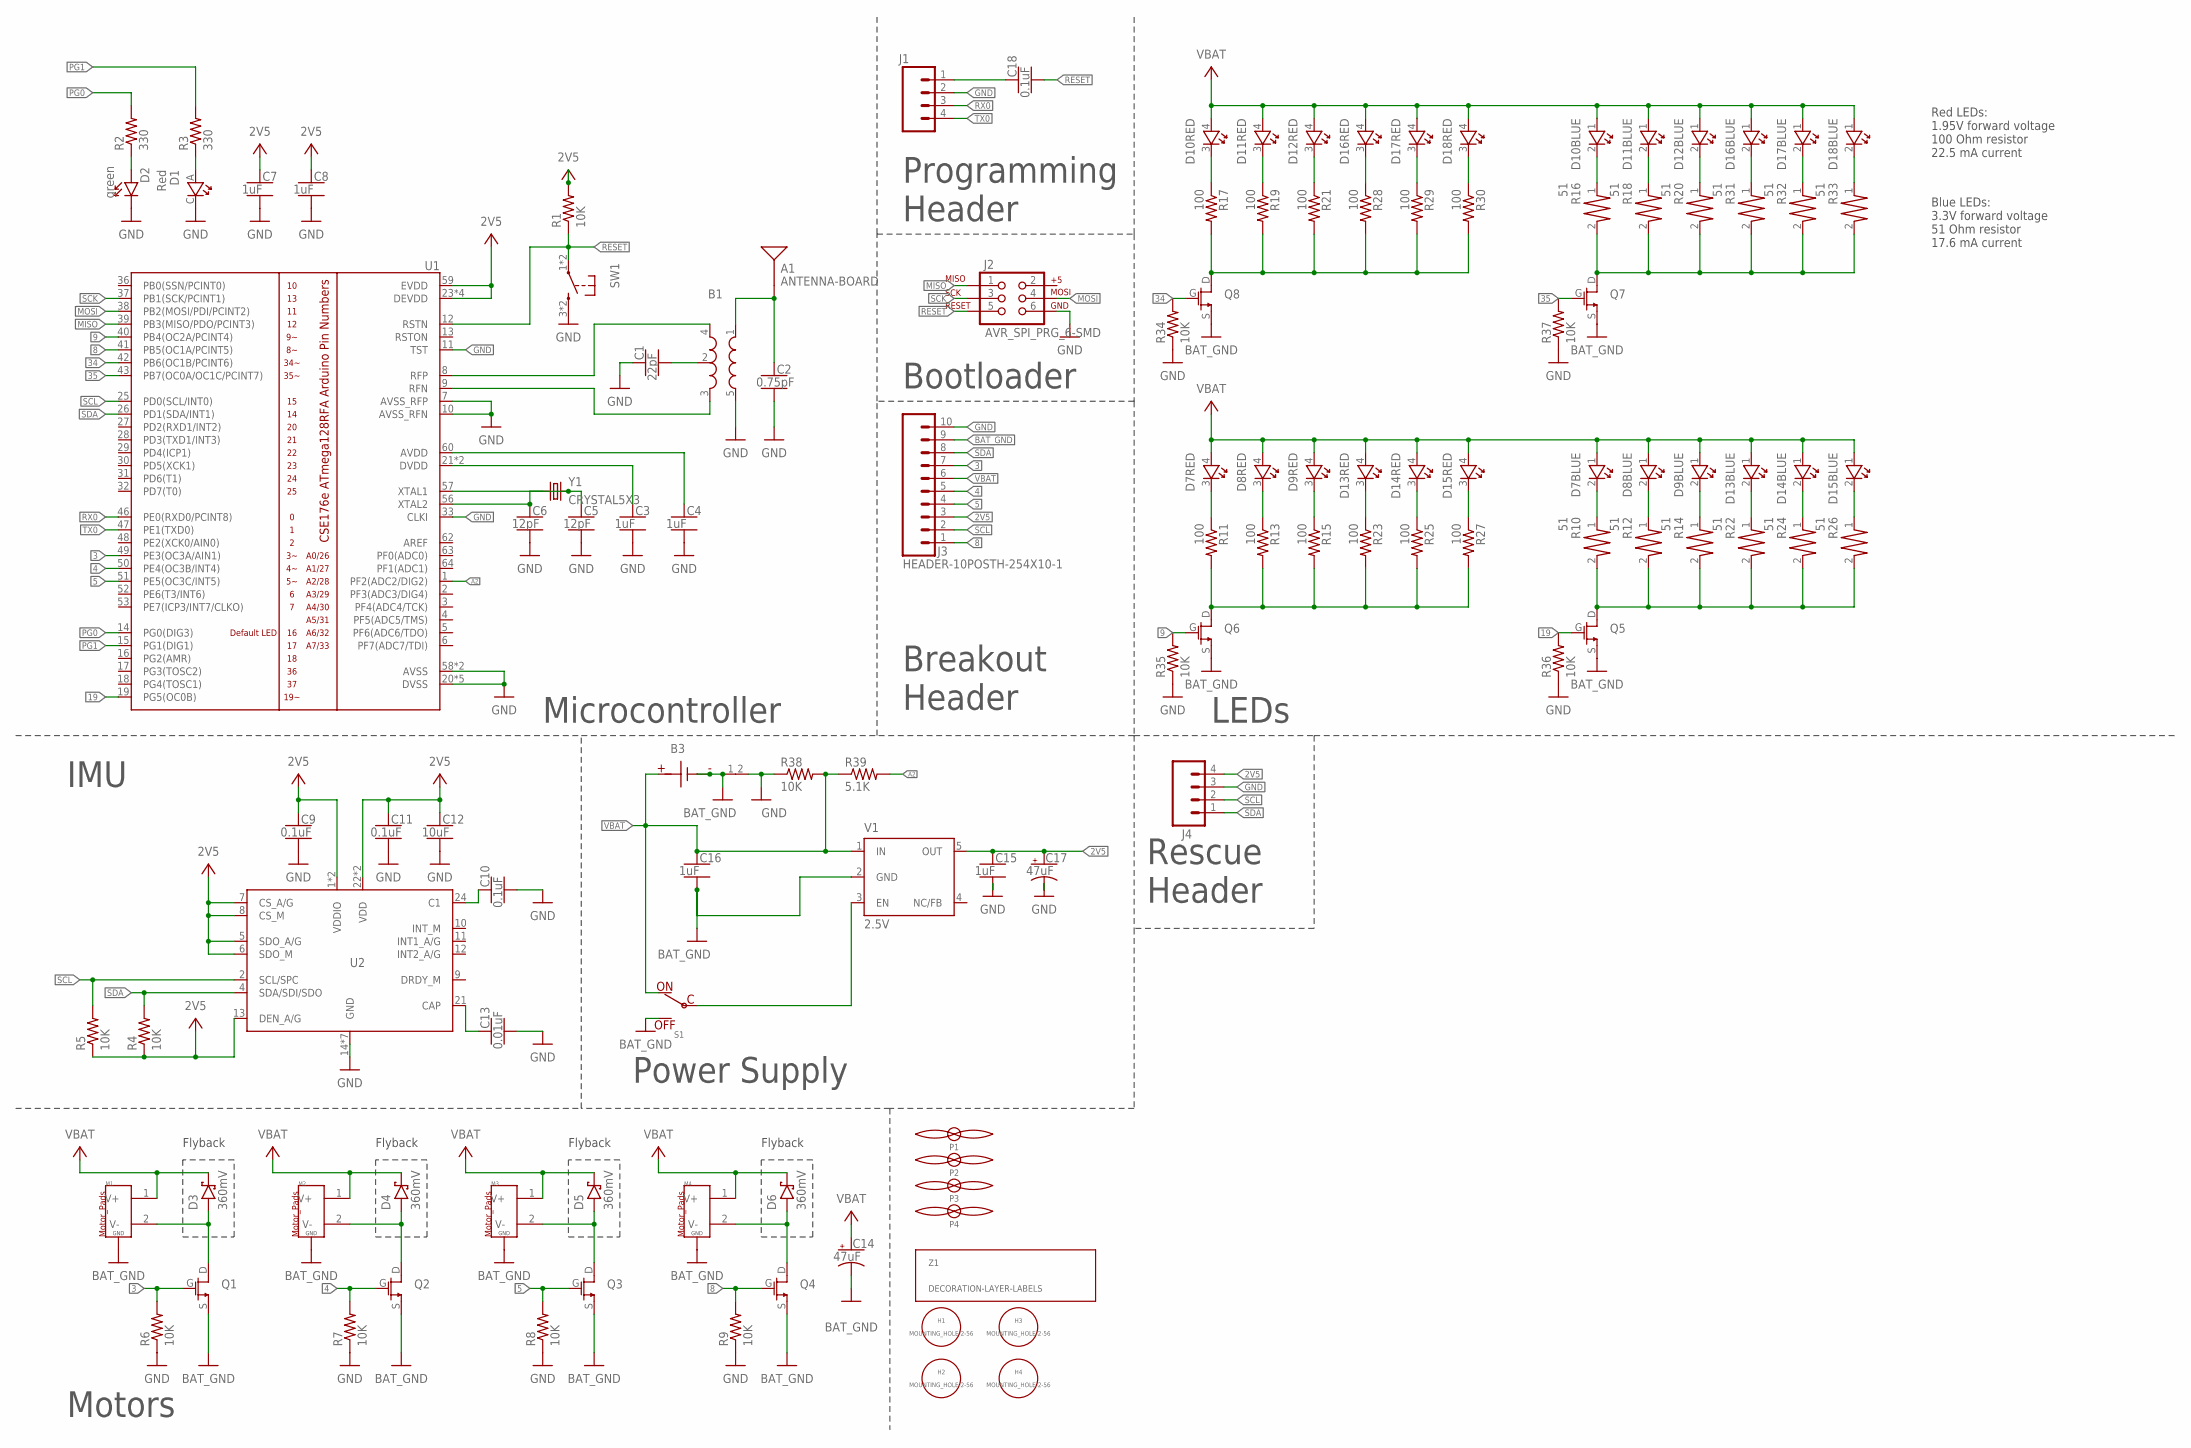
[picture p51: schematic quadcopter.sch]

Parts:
A1: ANTENNA-BOARD; ANT_PCB_2.4GHZ_NRF8001_1.6MM_1OZ
B1: BALUN0805; BALUN
B3: BATTERY-SMD-TH; BATTERY-COMBO
C1: 22pF; CAPC2012X140_HS
C2: 0.75pF; CAPC2012X140_HS
C3, C4, C7, C8, C15, C16: 1uF; CAPC2012X140_HS
C5, C6: 12pF; CAPC2012X140_HS
C9, C10, C11, C18: 0.1uF; CAPC2012X140_HS
C12: 10uF; CAPC2012X140_HS
C13: 0.01uF; CAPC2012X140_HS
C14, C17: 47uF; CAPMP3216X180
D1: Red; 0805_LED
D2: green; LEDSC125X200X120-2_HS
D3, D4, D5, D6: 360mV; SODFL3516X96
D7, D8, D9, D10, D11, D12, D13, D14, D15, D16, D17, D18: DUAL_LED0805_RB_LED; 0805_RB_LED
H1, H2, H3, H4: MOUNTING_HOLE-2-56; 2-56-MOUNTING-HOLE-NO-METAL
J1: HEADER-4POS-0.1IN-FEMALE-SMD-BOTTOM-ENTRY; HEADER-1X4-BOTTOM-ENTRY
J2: AVR_SPI_PRG_6-SMD; 2X3-SMD
J3: HEADER-10POSTH-254X10-1; HDRV10W63P254_10X1_2540X254H838_HS
J4: HEADER-4POS-0.1IN-FEMALE; HDRVR4W80P254_1X4_1066X254X850B
M1, M2, M3, M4: MOTOR_PADS_GND-MOLEX-SMD; MOLEX-0532610271
P1, P2, P3, P4: PROPELLOR-45MM; MOTOR_AND_PROP
Q1, Q2, Q3, Q4, Q5, Q6, Q7, Q8: NMOSFETSI2302CDS-T1-E3CT-ND; SOT23_MOSFET
R1, R4, R5, R6, R7, R8, R9, R34, R35, R36, R37, R38: 10K; RESC2012X60_HS
R2, R3: 330; RESC2012X60_HS
R10, R12, R14, R16, R18, R20, R22, R24, R26, R31, R32, R33: 51; 0805_RESISTOR
R11, R13, R15, R17, R19, R21, R23, R25, R27, R28, R29, R30: 100; RESC2012X60_HS
R39: 5.1K; RESC2012X60_HS
S1: POWER-SWITCH-MFS201N-9-Z-SMD-EDGE; JS102011SAQN
SW1: PUSHBUTTON_-4.5X4.5; 4.5MM_TACTILE_SWITCH_TL3305AF160QG
U1: ATMEGA128RFA1; QFN-64
U2: IMU_LSM9DS1LSM9DS1; IMU_LSM9DS1
V1: 2.5V; SOT23-DBV
W1: NET_BRIDGENET_BRIDGE; NET_BRIDGE
Y1: CRYSTAL5X3; CRYSTAL-SMD-5X3
Z1: DECORATION-LAYER-LABELS; LAYER_LABELS

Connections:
2V5: C7.1, C8.1, C9.1, C11.1, C12.1, C15.1, C17.1 (+), J3.3, J4.4, R1.2, R4.1, R5.1, U1.23 (DEVDD), U1.34 (DEVDD), U1.44 (DEVDD), U1.54 (DEVDD), U1.59 (EVDD), U2.1 (VDDIO), U2.3 (VDDIO), U2.5 (SDO_A/G), U2.6 (SDO_M), U2.7 (CS_A/G), U2.8 (CS_M), U2.13 (DEN_A/G), U2.22 (VDD), U2.23 (VDD), V1.5 (OUT)
3: J3.7, Q1.G, R6.2, U1.49 (PE3(OC3A/AIN1))
4: J3.5, Q2.G, R7.2, U1.50 (PE4(OC3B/INT4))
5: J3.4, Q3.G, R8.2, U1.51 (PE5(OC3C/INT5))
8: J3.1, Q4.G, R9.2, U1.41 (PB5(OC1A/PCINT5))
9: Q6.G, R35.2, U1.40 (PB4(OC2A/PCINT4))
19: Q5.G, R36.2, U1.19 (PG5(OC0B))
34: Q8.G, R34.2, U1.42 (PB6(OC1B/PCINT6))
35: Q7.G, R37.2, U1.43 (PB7(OC0A/OC1C/PCINT7))
A2: R39.2, U1.1 (PF2(ADC2/DIG2))
ADRV: A1.FEED, B1.1 (IN), C2.1
BAT_GND: B3.2 (N), B3.G (N), B3.G2 (N), B3.G3 (N), C14.2 (-), C16.2, J3.9, M1.G1 (GND), M1.G2 (GND), M2.G1 (GND), M2.G2 (GND), M3.G1 (GND), M3.G2 (GND), M4.G1 (GND), M4.G2 (GND), Q1.S, Q2.S, Q3.S, Q4.S, Q5.S, Q6.S, Q7.S, Q8.S, S1.A (OFF), V1.2 (GND), W1.1 (PAD_1)
GND: B1.5 (GND), C1.1, C2.2, C3.2, C4.2, C5.2, C6.2, C7.2, C8.2, C9.2, C10.2, C11.2, C12.2, C13.2, C15.2, C17.2 (-), D1.C, D2.C, J1.2, J2.6, J3.10, J4.3, R6.1, R7.1, R8.1, R9.1, R34.1, R35.1, R36.1, R37.1, R38.1, SW1.3 (2), SW1.4 (2), U1.7 (AVSS_RFP), U1.10 (AVSS_RFN), U1.11 (TST), U1.20 (DVSS), U1.24 (DVSS), U1.33 (CLKI), U1.35 (DVSS), U1.45 (DVSS), U1.55 (DVSS), U1.58 (AVSS), U1.61 (AVSS), U2.14 (GND), U2.15 (GND), U2.16 (GND), U2.17 (GND), U2.18 (GND), U2.19 (GND), U2.20 (GND), W1.2 (PAD_2)
MISO: J2.1, U1.39 (PB3(MISO/PDO/PCINT3))
MOSI: J2.4, U1.38 (PB2(MOSI/PDI/PCINT2))
unnamed: S1.C, V1.3 (EN)
unnamed: B1.2 (GND), C1.2
unnamed: C4.1, U1.60 (AVDD)
unnamed: C3.1, U1.21 (DVDD), U1.22 (DVDD)
unnamed: C5.1, U1.57 (XTAL1), Y1.3 (2)
unnamed: C6.1, U1.56 (XTAL2), Y1.1
unnamed: D2.A, R2.1
unnamed: D1.A, R3.1
unnamed: D3.2 (A), M1.2 (V-), Q1.D
unnamed: C10.1, U2.24 (C1)
unnamed: D4.2 (A), M2.2 (V-), Q2.D
unnamed: C13.1, U2.21 (CAP)
unnamed: D5.2 (A), M3.2 (V-), Q3.D
unnamed: D6.2 (A), M4.2 (V-), Q4.D
unnamed: D10.3 (C), R17.1
unnamed: D7.3 (C), R11.1
unnamed: Q8.D, R17.2, R19.2, R21.2, R28.2, R29.2, R30.2
unnamed: Q5.D, R10.2, R12.2, R14.2, R22.2, R24.2, R26.2
unnamed: D7.2 (C), R10.1
unnamed: Q6.D, R11.2, R13.2, R15.2, R23.2, R25.2, R27.2
unnamed: Q7.D, R16.2, R18.2, R20.2, R31.2, R32.2, R33.2
unnamed: D8.3 (C), R13.1
unnamed: C18.1, J1.1
unnamed: D8.2 (C), R12.1
unnamed: D13.3 (C), R23.1
unnamed: D9.3 (C), R15.1
unnamed: D10.2 (C), R16.1
unnamed: D9.2 (C), R14.1
unnamed: D13.2 (C), R22.1
unnamed: D14.3 (C), R25.1
unnamed: D11.3 (C), R19.1
unnamed: D11.2 (C), R18.1
unnamed: D12.3 (C), R21.1
unnamed: D12.2 (C), R20.1
unnamed: D14.2 (C), R24.1
unnamed: D15.3 (C), R27.1
unnamed: D15.2 (C), R26.1
unnamed: D16.3 (C), R28.1
unnamed: D17.3 (C), R29.1
unnamed: D18.3 (C), R30.1
unnamed: D16.2 (C), R31.1
unnamed: D17.2 (C), R32.1
unnamed: D18.2 (C), R33.1
PG0: R2.2, U1.14 (PG0(DIG3))
PG1: R3.2, U1.15 (PG1(DIG1))
RESET: C18.2, J2.5, R1.1, SW1.1, SW1.2 (1), U1.12 (RSTN)
RF_N: B1.3 (OUT2), U1.9 (RFN)
RF_P: B1.4 (OUT1), U1.8 (RFP)
RX0: J1.3, U1.46 (PE0(RXD0/PCINT8))
SCK: J2.3, U1.37 (PB1(SCK/PCINT1))
SCL: J3.2, J4.2, R5.2, U1.25 (PD0(SCL/INT0)), U2.2 (SCL/SPC)
SDA: J3.8, J4.1, R4.2, U1.26 (PD1(SDA/INT1)), U2.4 (SDA/SDI/SDO)
TX0: J1.4, U1.47 (PE1(TXD0))
VBAT: B3.1, B3.P, C14.1 (+), C16.1, D3.1 (C), D4.1 (C), D5.1 (C), D6.1 (C), D7.1 (A), D7.4 (A), D8.1 (A), D8.4 (A), D9.1 (A), D9.4 (A), D10.1 (A), D10.4 (A), D11.1 (A), D11.4 (A), D12.1 (A), D12.4 (A), D13.1 (A), D13.4 (A), D14.1 (A), D14.4 (A), D15.1 (A), D15.4 (A), D16.1 (A), D16.4 (A), D17.1 (A), D17.4 (A), D18.1 (A), D18.4 (A), J3.6, M1.1 (V+), M2.1 (V+), M3.1 (V+), M4.1 (V+), R38.2, R39.1, S1.B (ON), V1.1 (IN)

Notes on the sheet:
Microcontroller
Programming Header
IMU
Bootloader
Flyback
Breakout Header
Power Supply
Motors
LEDs
Red LEDs: 1.95V forward voltage 100 Ohm resistor 22.5 mA current
Blue LEDs: 3.3V forward voltage 51 Ohm resistor 17.6 mA current
Rescue Header

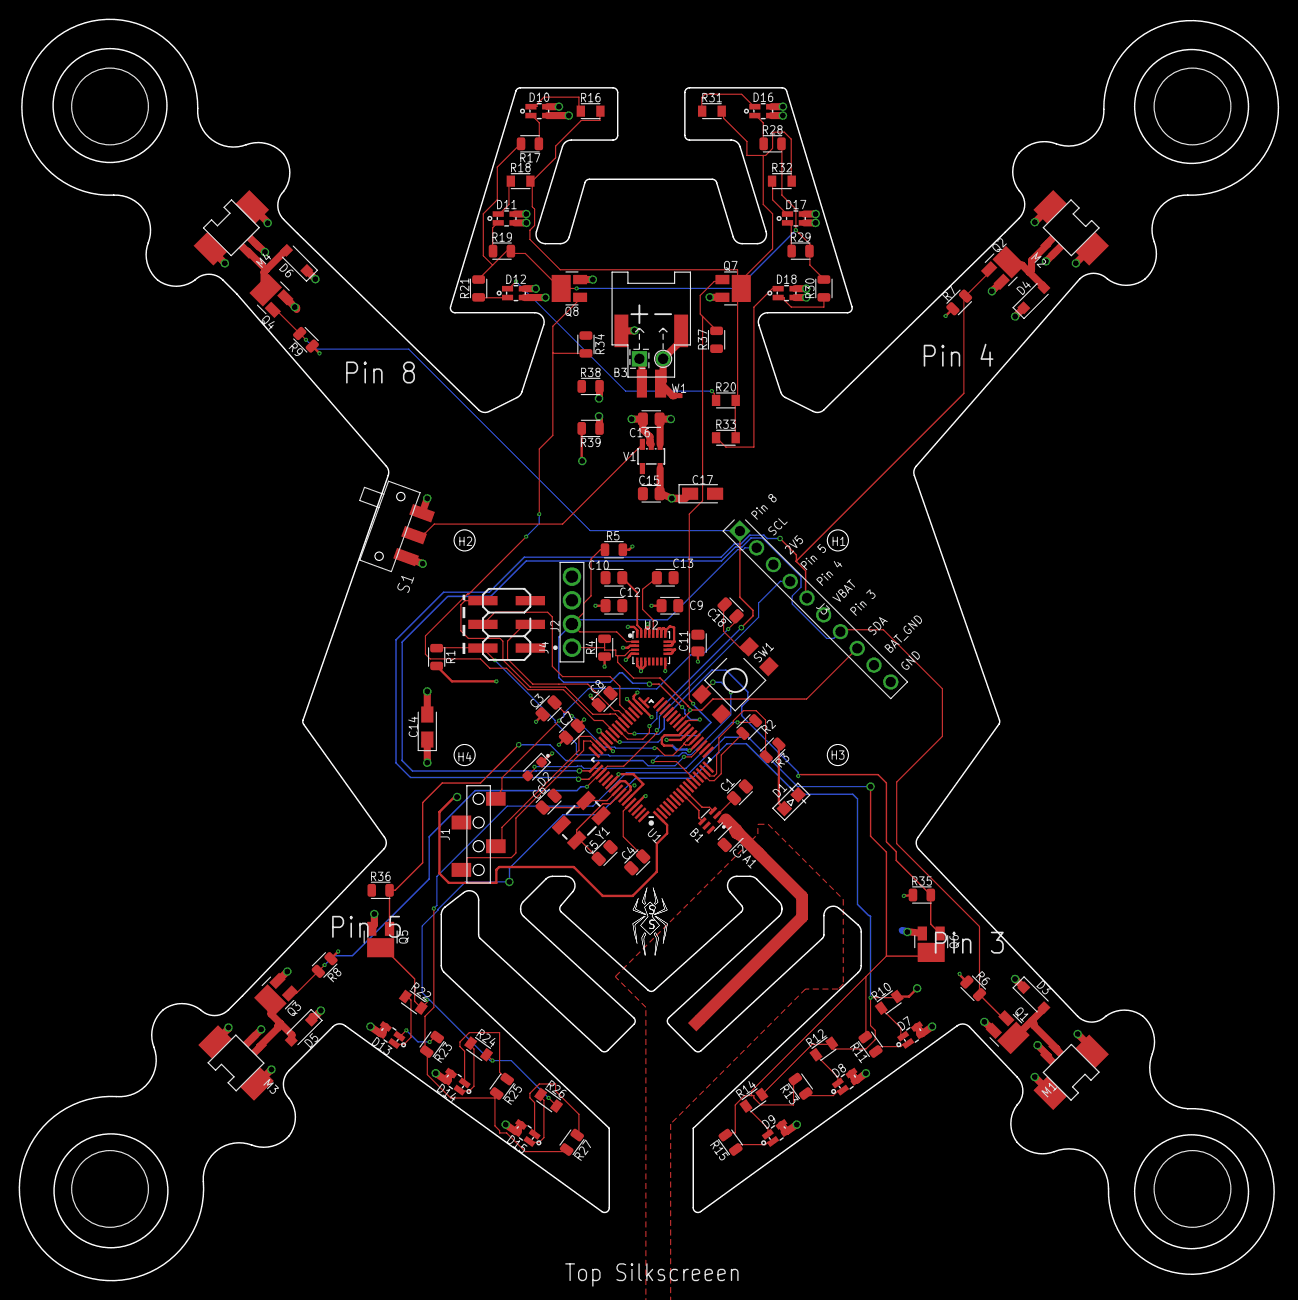
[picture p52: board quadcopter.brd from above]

Board: 4 copper layers, 134.9 x 135.2 mm, 112 parts (0 on the bottom side), 69 nets.

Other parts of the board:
L1, L2: DECORATIONSNEAKYSNAP; SNEAKYSNAP_LOGO

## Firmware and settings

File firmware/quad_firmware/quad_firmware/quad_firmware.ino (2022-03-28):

#include <radio.h>
#include <CommPacket.h>
#include <Logger.h>
#include <Despiker.h>
#include <EEPROM.h>

// Libraries required for getting the data from the IMU
#include <Wire.h>
#include <Adafruit_Sensor.h>
#include <Adafruit_LSM9DS1.h>
#include <Adafruit_Simple_AHRS.h>

// Defining the constants used by the LSM9DS1 (IMU)
#define FDS (1 << 2)

//Constants
#define FRONT_LEFT_MOTOR_PIN 4
#define BACK_RIGHT_MOTOR_PIN 5
#define BACK_LEFT_MOTOR_PIN 3
#define FRONT_RIGHT_MOTOR_PIN 8

const unsigned long TELEMETRY_PERIOD_MS = 100;
const unsigned long NO_PACKET_DISARM_TIMEOUT = 600;

// EVERYTHING CLOCKWISE POSITIVE
// LIKE FOR REAL EVERYTHING
// CHECK!
// Pitch axis: look down the stick with battery connector on the right (i.e. look from the quadcopter's right)
// Roll axis: look from the front
// Yaw axis: look from the top
const int PITCH_RATE_GYRO_SIGN = 1;
const int PITCH_ACCEL_SIGN = 1;
const int ROLL_RATE_GYRO_SIGN = 1;
const int ROLL_ACCEL_SIGN = 1;
const int YAW_RATE_SIGN = 1;

// For calibration
const int CALIBRATION_SAMPLES = 200;
const int CALIBRATION_DISCARD_SAMPLES = 100;
const int CALIBRATION_PERIOD_MS = 4;

const float GYRO_SPIKE_SIZE = 16;
const float MAX_ERROR_INTEGRAL = 100;

// Creating an instance lsm for communicating with the IMU using I2C
Adafruit_LSM9DS1 lsm = Adafruit_LSM9DS1();
Adafruit_Simple_AHRS ahrs(&lsm.getAccel(), &lsm.getMag(), &lsm.getGyro());

// Memory for the offsets
float pitch_accel_offset = 0.0;
float pitch_rate_gyro_offset = 0.0;
float roll_accel_offset = 0.0;
float roll_rate_gyro_offset = 0.0;
float yaw_rate_gyro_offset = 0.0;

// Memory for the estimated data and combination
float pitch = 0.00;
float roll = 0.00;
float yaw_rate = 0.00;

// Despikers
Despiker pitch_despiker = Despiker(GYRO_SPIKE_SIZE);
Despiker roll_despiker = Despiker(GYRO_SPIKE_SIZE);
Despiker yaw_despiker = Despiker(GYRO_SPIKE_SIZE);

// Memory for the PID loop
struct PIDMemory {
  float last_error;
  float error_integral;
};
PIDMemory pitch_memory;
PIDMemory yaw_memory;
PIDMemory roll_memory;

// Parameter values
ParameterValues parameters;

// The most recently recieved valid packet
Packet active_packet;

struct MotorOutputs {
  int front_left;
  int front_right;
  int back_left;
  int back_right;
};

const MotorOutputs OFF = {0, 0, 0, 0};

// Whether the quad is currently armed
bool armed;

// Last time a telemetry packet was sent
unsigned long last_telemetry_time = 0;
// Last time a packet was recieved from the remote
unsigned long last_packet_time = 0;
// Last time we read the data from IMU
unsigned long last_imu_time = 0;
// Last time we ran PID
unsigned long last_PID_time = 0;

// Logging
Logger dt_logger = Logger("time");

Logger yaw_rate_logger = Logger("yaw_rate");
Logger pitch_logger = Logger("pitch");
Logger roll_logger = Logger("roll");

Logger pitch_term_logger = Logger("pitch_term");
Logger roll_term_logger = Logger("roll_term");
Logger yaw_term_logger = Logger("yaw_term");

Logger pitch_integral_logger = Logger("pitch_integral");
Logger roll_integral_logger = Logger("roll_integral");
Logger yaw_integral_logger = Logger("yaw_integral");

Logger pitch_error_logger = Logger("pitch_error");
Logger roll_error_logger = Logger("roll_error");
Logger yaw_error_logger = Logger("yaw_error");

Logger pitch_derivative_logger = Logger("pitch_derivative");
Logger roll_derivative_logger = Logger("roll_derivative");
Logger yaw_derivative_logger = Logger("yaw_derivative");

Logger pitch_gyro_logger = Logger("pitch_rate_gyro");
Logger raw_pitch_gyro_logger = Logger("raw_pitch_gyro");
Logger pitch_accel_logger = Logger("pitch_accel");
Logger pitch_rate_offset_logger = Logger("pitch_rate_gyro_offset");

Logger roll_gyro_logger = Logger("roll_rate_gyro");
Logger roll_accel_logger = Logger("roll_accel");

Logger raw_yaw_gyro_logger = Logger("raw_yaw_gyro");

Logger throttle_overconstrain_logger = Logger("throttle_overconstrain");
Logger throttle_logger = Logger("throttle");

float pitch_err = 0.0;
float roll_err = 0.0;
float yaw_err = 0.0;

// EEPROM addresses
const int PARAMETER_EEPROM_ADDR = 0;

void setup() {
  const int SERIAL_BAUD = 19200;       // Baud rate for serial port
  Serial.begin(SERIAL_BAUD);           // Start up serial
  pinMode(LED_BUILTIN, OUTPUT);
  rfBegin(12);
  
  run_motors(OFF,false,0);
  armed = false;
  EEPROM.get(PARAMETER_EEPROM_ADDR, parameters);
  

  // Reset trims
//  parameters.pitch_values.trim = 0;
//  parameters.roll_values.trim = 0;
//  parameters.yaw_values.trim = 0;
  
  begin_i2c();                        // This will begin the communication between IMU and Arduino  
  setup_imu();                        // This is used to setup the IMU

  create_offset();
  
  send_telemetry();

  dt_logger.setEnable(false);

  const bool LOG_PITCH = false;
  const bool LOG_ROLL = false;
  const bool LOG_YAW = false;
  
  pitch_logger.setEnable(LOG_PITCH);
  roll_logger.setEnable(LOG_ROLL);
  yaw_rate_logger.setEnable(LOG_YAW);

  
  pitch_term_logger.setEnable(LOG_PITCH);
  roll_term_logger.setEnable(LOG_ROLL);
  yaw_term_logger.setEnable(LOG_YAW);

  pitch_integral_logger.setEnable(LOG_PITCH);
  roll_integral_logger.setEnable(LOG_ROLL);
  yaw_integral_logger.setEnable(LOG_YAW);
  
  pitch_error_logger.setEnable(LOG_PITCH);
  roll_error_logger.setEnable(LOG_ROLL);
  yaw_error_logger.setEnable(LOG_YAW);
  
  pitch_derivative_logger.setEnable(LOG_PITCH);
  roll_derivative_logger.setEnable(LOG_ROLL);
  yaw_derivative_logger.setEnable(LOG_YAW);
  
  
  const bool LOG_THROTTLE = false;
  throttle_overconstrain_logger.setEnable(LOG_THROTTLE);
  throttle_logger.setEnable(LOG_THROTTLE);

  pitch_gyro_logger.setEnable(false);
  pitch_accel_logger.setEnable(false);
  raw_pitch_gyro_logger.setEnable(false);
  pitch_rate_offset_logger.setEnable(false);

  roll_accel_logger.setEnable(false);
  roll_gyro_logger.setEnable(false);

  raw_yaw_gyro_logger.setEnable(false);
  
  last_PID_time = millis();
}


void loop() 
{
  // Clear for logging
  Serial.println("");
  
  read_radio();
  check_packet_timeout();
  send_telemetry_timed();
  read_imu_data();

  MotorOutputs motor_outputs;
  calc_PID(motor_outputs);
//  motor_outputs = {active_packet.throttle, active_packet.throttle, active_packet.throttle, active_packet.throttle};

  if (armed && active_packet.throttle != 0) {
    run_motors(motor_outputs, isSingleMotor(active_packet), getSelectedMotor(active_packet));
  } else {
    run_motors(OFF, false, 0);
  }
}

void begin_i2c()
{
  if(!lsm.begin())
  {
    // There was a problem detecting the LSM9DS0 ... check your connections
    Serial.print(F("Ooops, no LSM9DS1 detected ... Check your wiring or I2C ADDR!"));
    while(1);
    delay(10);
  }
}

/*
 * This is the function to set up the IMU
 * This will help us how we want our IMU to work.
 * What parts of IMU data we want to gets
 * Like the mangnetameter and gyroscope
 */
void setup_imu()
{
  const byte ODR = ODR_476;
  const byte G_HP_D = B00000000;
  // Set data rate for G and XL.  Set G low-pass cut off.  (Section 7.12)
  // LSM9DS1_REGISTER_CTRL_REG1_G         = 0x10,
  // This gives us the value that we are using the CTRL_REG1_G(10h)
  // The ODR frequency of 238hz ODR + 63Hz cuttof
  lsm.write8(XGTYPE, Adafruit_LSM9DS1::LSM9DS1_REGISTER_CTRL_REG1_G, ODR | G_BW_G_00 );
  lsm.write8(XGTYPE, Adafruit_LSM9DS1::LSM9DS1_REGISTER_CTRL_REG2_G, G_OUTSEL_HP_LP);
  lsm.write8(XGTYPE, Adafruit_LSM9DS1::LSM9DS1_REGISTER_CTRL_REG3_G, G_HP_D);
//  lsm.write8(XGTYPE, Adafruit_LSM9DS1::LSM9DS1_REGISTER_CTRL_REG3_G, G_HP_EN | parameters.gyro_highpass);


  // Enable the XL (Section 7.23)
  lsm.write8(XGTYPE, Adafruit_LSM9DS1::LSM9DS1_REGISTER_CTRL_REG5_XL, XL_ENABLE_X | XL_ENABLE_Y | XL_ENABLE_Z);

  // Set XL ODR
  lsm.write8(XGTYPE, Adafruit_LSM9DS1::LSM9DS1_REGISTER_CTRL_REG6_XL, ODR);

  // Set low-pass XL filter frequency divider (Section 7.25)
  // HR_MODE will turn on high resolution mode  
  // The High Pass Filter in LSM9DS1_REGISTER_CTRL_REG7_XL is already turned on
  // LSM9DS1_REGISTER_CTRL_REG7_XL come with FDS=0 but we turn it on using BW_SCAL_ODR.
  lsm.write8(XGTYPE, Adafruit_LSM9DS1::LSM9DS1_REGISTER_CTRL_REG7_XL, HR_MODE | parameters.accel_lowpass_ratio << 5);
  
  // enable mag continuous (Section 8.7)
  // We don't need magnetic sensor so we turn it off by doing B00000010 or B00000011
  lsm.write8(MAGTYPE, Adafruit_LSM9DS1::LSM9DS1_REGISTER_CTRL_REG3_M, B00000011);

  // This only sets range of measurable values for each sensor.  Setting these manually (I.e., without using these functions) will cause incorrect output from the library.
  lsm.setupAccel(Adafruit_LSM9DS1::LSM9DS1_ACCELRANGE_2G);
  lsm.setupMag(Adafruit_LSM9DS1::LSM9DS1_MAGGAIN_4GAUSS);
  lsm.setupGyro(Adafruit_LSM9DS1::LSM9DS1_GYROSCALE_2000DPS);
}

/*
 * Use this function to as a complementary filter
 * Will update according to the message received from the IC
 */
float complementary_filter(float filtered, float accel_heading, float gyro_heading_rate, float delta_time_seconds){
  // The complementary filters uses the weights
  // This helps us in defining how much importance should be given.
  // To gyroscope and accelerometer
  return (parameters.complementary)*(filtered + (delta_time_seconds*gyro_heading_rate)) + (1.0 - parameters.complementary) * accel_heading;
}

/**
 * Read a new packet from the radio buffer into active_packet, if one's arrived
 */
void read_radio() {
  int len;
  uint8_t b[sizeof(active_packet)];
  
  len = rfAvailable();
  if (len >= sizeof(active_packet)) {
    rfRead(b, sizeof(active_packet));
    if (checkPacket(((Packet*) b)[0])) {
      active_packet = ((Packet*) b)[0];
      armed = isArmed(active_packet);
      last_packet_time = millis();
      setParametersFromPacket(active_packet, parameters);
      if (getSelectedParameter(active_packet) == XL_LOWPASS) {
        lsm.write8(XGTYPE, Adafruit_LSM9DS1::LSM9DS1_REGISTER_CTRL_REG7_XL, HR_MODE | parameters.accel_lowpass_ratio << 5);
      } //else if (getSelectedParameter(active_packet) == GYRO_HIGHPASS) {
        //lsm.write8(XGTYPE, Adafruit_LSM9DS1::LSM9DS1_REGISTER_CTRL_REG3_G, G_HP_EN | parameters.gyro_highpass);
      //}
    } else {
      // Clear buffer if we get a bad packet, to avoid misalignment
      rfFlush();
    }
  }
}

/**
 * Check if it's been too long since the quad recieved a packet from the remote, and disarm if so
 */
void check_packet_timeout() {
  if (millis() - last_packet_time >= NO_PACKET_DISARM_TIMEOUT) {
    armed = false;
    EEPROM.put(PARAMETER_EEPROM_ADDR, parameters);
    // Send telemetry immediately to broadcast the disarm
    send_telemetry();
  }
}

/*
 * This particular function of the code is useful for creating the offset
 * Assuming we start every flight from a flat surface
 * If this is not the case, we will hard code the offsets in our code.
 * The values are as follows:-
 * acc_pitch_offset = 1.16;
 * gyro_pitch_rate_offset = 2.62;
 */
void create_offset() {
  quad_data_t orientation;
  int samples = 0;

  float pitch_accel_sum = 0;
  float pitch_gyro_sum = 0;
  float roll_accel_sum = 0;
  float roll_gyro_sum = 0;
  float yaw_gyro_sum = 0;

  while (samples < CALIBRATION_DISCARD_SAMPLES) {
      if (ahrs.getQuadOrientation(&orientation)) {
        samples += 1;
      }
      delay(CALIBRATION_PERIOD_MS);
  }

  samples = 0;
  
  while (samples < CALIBRATION_SAMPLES) {
      if (ahrs.getQuadOrientation(&orientation)) {
//        pitch_accel_sum += orientation.roll;
//        pitch_gyro_sum += pitch_despiker.despike(orientation.roll_rate);
//        roll_accel_sum += orientation.pitch;
//        roll_gyro_sum += roll_despiker.despike(orientation.pitch_rate);
//        yaw_gyro_sum += yaw_despiker.despike(orientation.yaw_rate);
        samples += 1;
      }
      delay(CALIBRATION_PERIOD_MS);
  }
  
  pitch_accel_offset = pitch_accel_sum / CALIBRATION_SAMPLES;
  pitch_rate_gyro_offset = pitch_gyro_sum / CALIBRATION_SAMPLES;
//  pitch_rate_gyro_offset = 0;
  roll_accel_offset = roll_accel_sum / CALIBRATION_SAMPLES;
  roll_rate_gyro_offset = roll_gyro_sum / CALIBRATION_SAMPLES;
//  roll_rate_gyro_offset = 0;
  yaw_rate_gyro_offset = yaw_gyro_sum / CALIBRATION_SAMPLES;
//  yaw_rate_gyro_offset = 0;
//  Serial.print("ACC PITCH = "); Serial.println(pitch_accel_offset);
//  Serial.print("GYRO PITCH = "); Serial.println(pitch_rate_gyro_offset);
//  Serial.print("ACC ROLL = "); Serial.println(roll_accel_offset);
//  Serial.print("GYRO ROLL = "); Serial.println(roll_rate_gyro_offset);
//  Serial.print("GYRO YAW = "); Serial.println(yaw_rate_gyro_offset);
//  delay(1000);
}

void read_imu_data() {
  quad_data_t orientation;
  unsigned long current_imu_time = millis();
  /* 'orientation' should have valid .roll and .pitch fields */
  if (ahrs.getQuadOrientation(&orientation)) {
    
    float pitch_accel = (orientation.roll - pitch_accel_offset) * PITCH_ACCEL_SIGN;
    float roll_accel = (orientation.pitch - roll_accel_offset) * ROLL_ACCEL_SIGN;
    
    float pitch_rate_gyro = (orientation.roll_rate - pitch_rate_gyro_offset) * PITCH_RATE_GYRO_SIGN;
    float roll_rate_gyro = (orientation.pitch_rate - roll_rate_gyro_offset) * ROLL_RATE_GYRO_SIGN;
    yaw_rate = (orientation.yaw_rate - yaw_rate_gyro_offset) * YAW_RATE_SIGN;

    
    const float imu_read_time_seconds = (current_imu_time - last_imu_time) / 1000.0;
    pitch = complementary_filter(pitch, pitch_accel, pitch_rate_gyro, imu_read_time_seconds);
    roll = complementary_filter(roll, roll_accel, roll_rate_gyro, imu_read_time_seconds);

    dt_logger.log(current_imu_time - last_imu_time);
    yaw_rate_logger.log(yaw_rate);
    pitch_logger.log(pitch);
    roll_logger.log(roll);

    raw_pitch_gyro_logger.log(orientation.pitch_rate);
    raw_yaw_gyro_logger.log(orientation.yaw_rate);
    
    pitch_gyro_logger.log(pitch_rate_gyro);
    pitch_accel_logger.log(pitch_accel);
    pitch_rate_offset_logger.log(pitch_rate_gyro_offset);

    roll_accel_logger.log(roll_accel);
    roll_gyro_logger.log(roll_rate_gyro);
    
    last_imu_time = current_imu_time;
  }
}

/**
 * Send telemetry only if enough time has elapsed since the last telemetry packet
 */
void send_telemetry_timed(){
  if (millis() - last_telemetry_time >= TELEMETRY_PERIOD_MS) {
    send_telemetry();
  }
}


/**
 * Send telemetry data back to the remote
 */
void send_telemetry() {
  Telemetry telemetry;
  buildTelemetry(telemetry, armed, pitch_err, roll_err, yaw_err);
  rfWrite((byte*) &telemetry, sizeof(telemetry));
  last_telemetry_time = millis();
}


void calc_PID(MotorOutputs& motor_outputs) {
  unsigned long PID_time = millis();

  const float loop_time_seconds = (PID_time - last_PID_time) / 1000.0;

  // Clear windup
  if (active_packet.throttle == 0 ) {
    pitch_memory.error_integral = 0;
    yaw_memory.error_integral = 0;
    roll_memory.error_integral = 0;
  }
  // const float pitch_term = 0;
  // const float yaw_term = 0;
  // const float roll_term = 0;
  
  const float pitch_term = pure_PID(pitch, (active_packet.pitch + 0.0) / 5.35, loop_time_seconds, pitch_memory, parameters.pitch_values, pitch_err, pitch_derivative_logger);
  const float yaw_term = pure_PID(yaw_rate, (active_packet.yaw + 0.0)/0.7, loop_time_seconds, yaw_memory, parameters.yaw_values, yaw_err, yaw_derivative_logger);
  const float roll_term = pure_PID(roll, (active_packet.roll + 0.0)/5.35, loop_time_seconds, roll_memory, parameters.roll_values, roll_err, roll_derivative_logger);

  pitch_error_logger.log(pitch_err);
  roll_error_logger.log(roll_err);
  yaw_error_logger.log(yaw_err);
  // Serial.println();
  // Serial.print("Pitch: "); Serial.println(pitch_memory.error_integral);
  // Serial.print("Yaw: "); Serial.println(yaw_term);

  const int front_left_term = -pitch_term - yaw_term - roll_term;
  const int front_right_term = -pitch_term + yaw_term + roll_term;
  const int back_left_term = pitch_term + yaw_term - roll_term;
  const int back_right_term = pitch_term -  yaw_term + roll_term;

  const int max_throttle = 255 - max(max(max(max(0, front_left_term), front_right_term), back_left_term), back_right_term);
  const int min_throttle = -min(min(min(min(0, front_left_term), front_right_term), back_left_term), back_right_term);
  int mixed_throttle = 0;

  if (min_throttle > max_throttle) {
    // Average if the PID outputs require impossible throttle
    mixed_throttle = (min_throttle + max_throttle) / 2;
    throttle_overconstrain_logger.log(5);
  } else {
    mixed_throttle = map(active_packet.throttle, 0, 255, min_throttle, max_throttle);
    throttle_overconstrain_logger.log(0);
  }
  
  motor_outputs.front_left = constrain(mixed_throttle + front_left_term, 0, 255);
  motor_outputs.front_right = constrain(mixed_throttle + front_right_term, 0, 255);
  motor_outputs.back_left = constrain(mixed_throttle + back_left_term, 0, 255);
  motor_outputs.back_right = constrain(mixed_throttle + back_right_term, 0, 255);
  
  pitch_term_logger.log(pitch_term);
  roll_term_logger.log(roll_term);
  yaw_term_logger.log(yaw_term);
  throttle_logger.log(mixed_throttle);
  
  pitch_integral_logger.log(pitch_memory.error_integral);
  roll_integral_logger.log(roll_memory.error_integral);
  yaw_integral_logger.log(yaw_memory.error_integral);

  last_PID_time = PID_time;
}

/**
 * Calculate output from a PID loop. This is almost a "pure" function - the only side effect is modifying the PID memory.
 */
float pure_PID(float value, float setpoint, float delta_time, PIDMemory& memory, const PIDValues& gains, float& error, Logger& derivative_logger) {
  /*
  const float error = value - gains.trim - setpoint;
  float error_derivative = 0;
  if (abs(error) >= 1)
  {
    if(abs(error) > abs(memory.last_error))
    {
      memory.error_integral += error * delta_time;
    }
    error_derivative = (error - memory.last_error) / delta_time;
    memory.error_integral = min(memory.error_integral, 100);
  } else {
    error_derivative = 0;
    memory.error_integral = 0;
  }
  memory.last_error = error;
  */
  error = setpoint - (value - gains.trim);
  // LOGGING STATEMENT
//  telemetry_log_value = error;
  const float error_derivative = (error - memory.last_error) / delta_time;
  derivative_logger.log(error_derivative);
//  if (-3 < error < 3) {
  memory.error_integral += error * delta_time;
  memory.error_integral = constrain(memory.error_integral, -MAX_ERROR_INTEGRAL, MAX_ERROR_INTEGRAL);
//  }
  memory.last_error = error;
  
  return gains.p * error + gains.i * memory.error_integral + gains.d * error_derivative;
}

/**
 * Set the diplay LEDs on the quadcopter according to the current state
 */
void set_LEDs() {
  digitalWrite(LED_BUILTIN, armed ? HIGH : LOW);
}

/**
 * Run each of the motors at the specified speeds
 */
void run_motors(MotorOutputs outputs, bool single_motor, byte motor_select) {
  if (!single_motor || motor_select == FRONT_LEFT) {
    analogWrite(FRONT_LEFT_MOTOR_PIN, outputs.front_left);
  } else {
    analogWrite(FRONT_LEFT_MOTOR_PIN, 0);
  }
  if (!single_motor || motor_select == FRONT_RIGHT) {
    analogWrite(FRONT_RIGHT_MOTOR_PIN, outputs.front_right);
  } else {
    analogWrite(FRONT_RIGHT_MOTOR_PIN, 0);
  }
  if (!single_motor || motor_select == BACK_LEFT) {
    analogWrite(BACK_LEFT_MOTOR_PIN, outputs.back_left);
  } else {
    analogWrite(BACK_LEFT_MOTOR_PIN, 0);
  }
  if (!single_motor || motor_select == BACK_RIGHT) {
    analogWrite(BACK_RIGHT_MOTOR_PIN, outputs.back_right);
  } else {
    analogWrite(BACK_RIGHT_MOTOR_PIN, 0);
  }
}

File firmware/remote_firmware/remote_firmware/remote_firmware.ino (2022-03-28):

#include <radio.h>
#include "quad_remote.h"      // Header file with pin definitions and setup
#include <CommPacket.h>
#include <Debouncer.h>
#include <EEPROM.h>

// Constants
const int DEADBAND = 10;
const int PACKET_PERIOD_MS = 50;
const int CALIBRATION_TIMEOUT_MS = 5000; // How long to wait with no calibration value changes before telling the user they're done
const int DEBOUNCE_TIME_MS = 200;
const int NO_TELEMETRY_DISARM_TIMEOUT = 2000;
const float PID_ADJUSTMENT_GRANULARITY = 0.05;
const float TRIM_ADJUSTMENT_GRANULARITY = 1.0;


// States
const byte DISARMED = 0;
const byte CALIBRATION = 1;
const byte ARMED = 2;

// Parameter adjustment UI categories
const byte SENSING = 0;
const byte PITCH_LOOP = 1;
const byte ROLL_LOOP = 2;
const byte YAW_LOOP = 3;

const byte NUM_CATEGORIES = 4;

// Parameters
const byte P = 0;
const byte I = 1;
const byte D = 2;
// None is 0
const byte COMPLEMENTARY = 1;
const byte GYRO_HP = 2;
const byte XL_LP_RATIO = 3;

// struct for calibration values. rest_* means the value the stick has when it's not being touched.
struct CalibrationValues {
  int min_throttle;
  int max_throttle;
  int min_yaw;
  int rest_yaw;
  int max_yaw;
  int min_roll;
  int rest_roll;
  int max_roll;
  int min_pitch;
  int rest_pitch;
  int max_pitch;
};

CalibrationValues calibration;
ParameterValues parameters;


// Predeclarations for callback functions
void btn_one_pressed(bool down);
void btn_two_pressed(bool down);
void btn_up_pressed(bool down);
void btn_down_pressed(bool down);
void btn_left_pressed(bool down);
void btn_right_pressed(bool down);
void btn_center_pressed(bool down);

// State
byte state = DISARMED;

// Parameter selection
byte parameter_category;
byte selected_parameter;

// Scaled values for the axes
byte throttle_value;
int8_t yaw_value;
int8_t roll_value;
int8_t pitch_value;

// Raw values from the gimbals for each axis
int throttle_raw;
int yaw_raw;
int roll_raw;
int pitch_raw;

// For single motor mode, where only one motor on the quadcopter is run.
bool single_motor_mode = false;
byte motor_select = FRONT_LEFT;

// For trim UI
bool adjust_trim = false;
byte which_trim = PITCH_TRIM;

// Most recent telemetry data from the quadcopter
Telemetry active_telemetry;

// Local variables we don't want to reallocate every loop
Packet p;
uint8_t b[sizeof(active_telemetry)];
char newFirstLine[17];
char newSecondLine[17];

// Display strings
// 16 character wide, 2-line display
char displayLine1[17];
char displayLine2[17];
unsigned long displayRGB;

// Last time a packet was sent to the quadcopter
unsigned long last_send_time = 0;
// Last time the calibration data were updated.
unsigned long last_calibration_update = 0;
// For debouncing
Debouncer btn1_debouncer = Debouncer(DEBOUNCE_TIME_MS);
Debouncer btn2_debouncer = Debouncer(DEBOUNCE_TIME_MS);
Debouncer btn_left_debouncer = Debouncer(DEBOUNCE_TIME_MS);
Debouncer btn_right_debouncer = Debouncer(DEBOUNCE_TIME_MS);
Debouncer btn_up_debouncer = Debouncer(DEBOUNCE_TIME_MS);
Debouncer btn_center_debouncer = Debouncer(DEBOUNCE_TIME_MS);
Debouncer btn_down_debouncer = Debouncer(DEBOUNCE_TIME_MS);
Debouncer knob_debouncer = Debouncer(DEBOUNCE_TIME_MS);
// Last time a telemetry packet was recieved
unsigned long last_telemetry_time = 0;

// EEPROM addresses
const int CALIBRATION_EEPROM_ADDR = 0;
const int PARAMETER_EEPROM_ADDR = CALIBRATION_EEPROM_ADDR + sizeof(calibration);
const int PARAMETER_CATEGORY_EEPROM_ADDR = PARAMETER_EEPROM_ADDR + sizeof(parameters);
const int PARAMETER_SELECTION_EEPROM_ADDR = PARAMETER_CATEGORY_EEPROM_ADDR + sizeof(parameter_category);

void setup() {
  const int SERIAL_BAUD = 19200;        // Baud rate for serial port 
  Serial.begin(SERIAL_BAUD);           // Start up serial
  delay(100);
  quad_remote_setup();
  rfBegin(12);

  // Read EEPROM values
  EEPROM.get(CALIBRATION_EEPROM_ADDR, calibration);
  EEPROM.get(PARAMETER_EEPROM_ADDR, parameters);
  EEPROM.get(PARAMETER_CATEGORY_EEPROM_ADDR, parameter_category);
  EEPROM.get(PARAMETER_SELECTION_EEPROM_ADDR, selected_parameter);
//  parameters = {
//    {0.55,  0.10, 0.20, 0.0},     //pitch
//    {0.55,  0.10, 0.20, 0.0},     //roll
//    {3.3,   0.0,  5.0,  0.0},     //yaw
//    0.95,
//    B1001,
//    B00
//  };
  parameter_category = SENSING;
  selected_parameter = 0;

//  parameters.pitch_values.trim = 0;
//  parameters.roll_values.trim = 0;
//  parameters.yaw_values.trim = 0;
  

  state = DISARMED;
  // Button 1 is the calibration button
  btn1_cb = btn_one_pressed;
  btn2_cb = btn_two_pressed;
        
  knobs_update_cb = knobs_update; 
  knob1_btn_cb = knob_pressed;
  btn_up_cb =  btn_up_pressed;
  btn_down_cb = btn_down_pressed;
  btn_left_cb =  btn_left_pressed;
  btn_right_cb = btn_right_pressed;
  btn_center_cb = btn_center_pressed;
}

void loop() {
  read_gimbals();
  recieve_telemetry();
  check_telemetry_timeout();

  // State-dependent routines
  if (state == ARMED) {
    scale_gimbals();
  } else if (state == CALIBRATION) {
    do_calibration();
  } else if (state == DISARMED) {
    scale_gimbals();
    check_for_arm();
  }

  // Only send one packet per PACKET_PERIOD_MS
  if (millis() - last_send_time >  PACKET_PERIOD_MS) {
    send_packet();
  }

  set_display();
  delay(2);
}

/**
 * Toggle calibration mode. Resets saved calibration data when entering calibration mode.
 */
void btn_one_pressed(bool down) {
  // Only on-press
  if (!down || !btn1_debouncer.debounce()) {
    return;
  }
  
  if (state == DISARMED) {
    state = CALIBRATION;

    // Set this so display doesn't immediately prompt to end calibration
    last_calibration_update = millis();

    // Reset data and read rest values
    calibration = {
      throttle_raw,
      throttle_raw,
      yaw_raw,
      yaw_raw,
      yaw_raw,
      roll_raw,
      roll_raw,
      roll_raw,
      pitch_raw,
      pitch_raw,
      pitch_raw
    };
  } else if (state == CALIBRATION) {
    state = DISARMED;
    EEPROM.put(CALIBRATION_EEPROM_ADDR, calibration);
  }
}

void btn_two_pressed(bool down) {
  // Only on-press
  if (!down || !btn2_debouncer.debounce()) {
    return;
  }
  
  if (single_motor_mode && motor_select == FRONT_LEFT) {
    single_motor_mode = false;
  } else {
    single_motor_mode = true;
    motor_select = (motor_select + 1) & B00000011;
  }
}

void btn_left_pressed(bool down) {
  // Only on-press
  if (!down || !btn_left_debouncer.debounce()) {
    return;
  }

  if (adjust_trim) {
    which_trim = ROLL_TRIM;
    parameters.roll_values.trim -= TRIM_ADJUSTMENT_GRANULARITY;
  } else {
    if (parameter_category == 0) {
      parameter_category = NUM_CATEGORIES;
    }
    parameter_category = parameter_category - 1;
    
    // lower max to 2 in case we're switching from sensing to PID
    selected_parameter = constrain(selected_parameter, 0, 2);
    
    EEPROM.put(PARAMETER_CATEGORY_EEPROM_ADDR, parameter_category);
  }
}
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
